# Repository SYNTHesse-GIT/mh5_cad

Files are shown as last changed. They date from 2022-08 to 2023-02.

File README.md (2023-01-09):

# mh5_cad - CAD files, including STLs for MH5 robot



The 3D design of the robot is maintained in [onshape](https://cad.onshape.com/documents/1b88afa68bb97584375e284c/w/8d3aebf9e78687fc1b4a5d80/e/6f5b4ad05cdba68c2c42dd17).

The parts bellow are for the Revision F model of the MH5 humanoid robot.

## Printing BOM

| Item | Description | Final | Qty | Comments |
|---|---|---|-----|---|
| [Foot-Sole](STL/Foot-Sole.stl) | Sole for the FSR feet | Yes | 2 | one for each foot
| [Foot-Top](STL/Foot-Top.stl) | Upper part of FSR feel | Yes | 2 | one for each foot
| [Foot-Back](STL/Foot-Back.stl) | Back side of the FSR foot, uses magnets | Yes | 2 | one for each foot
| [Ankle](STL/Ankle.stl) | Frame for ankle | Yes | 4 | 2 for each foot
| [MH5-F02](STL/MH5-F02.stl) | Stright U frame | Yes | 4 | 2 used in feet (1 each) and 2 used in arms (1 each)
| [MH5-F03](STL/MH5-F03.stl) | Bottom of servo frame | Yes | 6 | 3 for each arm
| [MH5-F04](STL/MH5-F04.stl) | Curved U frame | Yes | 4 | 2 used in hips and 2 in shoulders
| [MH5-F05](STL/MH5-F05.stl) | Thigh frame | Yes | 2 | one in each foot
| [Hand-Left](STL/Hand-Left.stl) | Anatomic left hand | Yes | 1 |
| [Hand-Right](STL/Hand-Right.stl) | Anatomic right hand | Yes | 1 |
| [Chest](STL/Chest.stl) | Chest main frame | Yes | 1 |
| [Front](STL/Front.stl) | Front chest cover | Yes | 1 |
| [Neck](STL/Neck.stl) | Neck | Yes | 1 |
| [Head-Back](STL/Head-Back.stl) | Back side of the head | Yes | 1 |
| [Head-Front](STL/Head-Front.stl) | Front side of the head | Yes | 1 |
| [Head-Camera-Cover](STL/Head-Camera-Cover.stl) | Cover for cameras. | Yes | 2 | One for each mini camera

## Assembly preparation

Before assembly you must configure the Dynamixel Servos as described in [Configuring servos](DOCS/servos.md).

You should also get familiar with the [installation of heat-serts](DOCS/assembly-heatserts.md). There will several steps in the following instructions where you will have to perform this activity.

Quite a few number of servos in this robot make use of the new through-the-idler wiring of the cables that produces a tidier cabling and reduces the stress and the risk of cables being severed by frame collision. You should be familiar with the instructions provided by Robotis for both the [XL430](https://emanual.robotis.com/docs/en/dxl/x/xl430-w250/#idler-horn-assembly) and the [2XL430](https://emanual.robotis.com/docs/en/dxl/x/2xl430-w250/#idler-horn-assembly) servos.

## Sub-groups Assembly

[**Leg assembly**](DOCS/assembly-legs.md) is almost identical for left and right because the 2-axis servomotors make impossible mirror assembly. The only difference is the way the feet are connected to the ankles and this is explicitly described in the instructions.

[**Arms assembly**](DOCS/assembly-arms.md) is symmetrical so that cables are following a consistent pattern (on the inside or on the outside of the assembly, but similar between left and right). The instructions describe these activities in detail.

[**Torso and neck**](DOCS/assembly-torso.md) assembly describes the assembly of the fixed components to the torso.

In [**Full assembly**](DOCS/assembly-full.md) the sub-assemblies prepared earlier as well as the electronic components are put together to produce the full robot.

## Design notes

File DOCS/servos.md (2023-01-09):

# Configuring servos

Before assembling the robot, all servos need to be configured. Because they come with the same pre-configured IDs, once connected on a chain the servos cannot be accessed because of duplicate IDs. Therefore is it very important to update the IDs of all the servos *before* they are mounted on frames and connected with the cables. In addition to IDs we will also change the communication speed and a small amount of other parameters to simplify their management after assembly in the robot.

We use two models of Robotis servos: [XL430-W250](https://emanual.robotis.com/docs/en/dxl/x/xl430-w250/) and [2XL430-W250](https://emanual.robotis.com/docs/en/dxl/x/2xl430-w250/). Logically the two servos have identical control characteristics, with the main difference that 2XL430 has a dual axis construction, behaving as two XL430 servos in one. Most of the control registers are therefore presented in duplicate, one for each axis, with a few notable exceptions that we will highlight in the following instructions.

## Connecting the servos

In order to configure the servos we will use the [DynamixelWizard2](https://emanual.robotis.com/docs/en/software/dynamixel/dynamixel_wizard2/) application provided by Robotis. The application is available for Windows, Mac and Linux operating systems and should be downloaded and installed according to the instructions provided in the link above.

To connect the servos to the computer we recommend using an interface like [U2D2](https://emanual.robotis.com/docs/en/parts/interface/u2d2/) that connects to computers using standard USB ports and provides high-speed Dynamixel ports compatible with all Robotis servos.

> **Note:** <br>
> U2D2 does not provide power to the servos, only data control signals. In order to power the servos being configured you need to use an external power supply and an adapter board that makes that power available over the Dynamixel bus. Our recommendation is to use the [U2D2 Power Hub](https://emanual.robotis.com/docs/en/parts/interface/u2d2_power_hub/) which pairs conveniently with the U2D2 interface. Robotis also has a [Starter Set](http://en.robotis.com/shop_en/item.php?it_id=902-0161-200) that includes the U2D2 interface, the Power Hub and a 5A 12V power supply.

When configuring the servos, you should connect only one at a time, to avoid conflicts with duplicate IDs. Theoretically, once you have configured a servo, you could add a new by daisy-chaining it to the previous one as we're setting IDs above 10 and there will not be duplicates, but frankly there is no advantage for having multiple servos connected at this stage and you should anyway avoid constructing chains of more than 6 servos as you could experience a degradation of communication performance. We recommend connecting one servo for configuration and then removing it before connecting the next servo.

To connect the servos follow the diagram below:

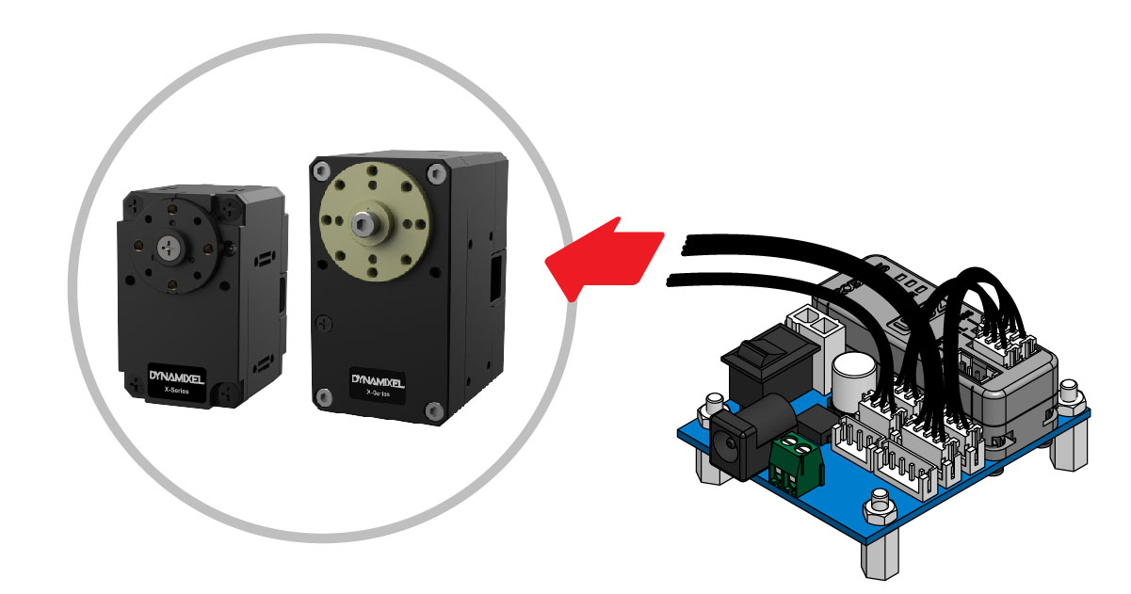
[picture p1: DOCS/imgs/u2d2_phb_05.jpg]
Connecting Servos


Servos have two connectors and any of them can be used to connect to the U2D2 interface.

The power supply should be connected to the DC plug on the Power Hub. The servo will indicate that has powered and is initialized successfully by short blinking the LED once. This LED should not be on continuously.

## DynamixelWizard setup

When first using the Dynamixel Wizard you will have to configure several settings like the communication port and the speed. Click the "Options" button in the toolbar:

Options

This will open the following dialog window:

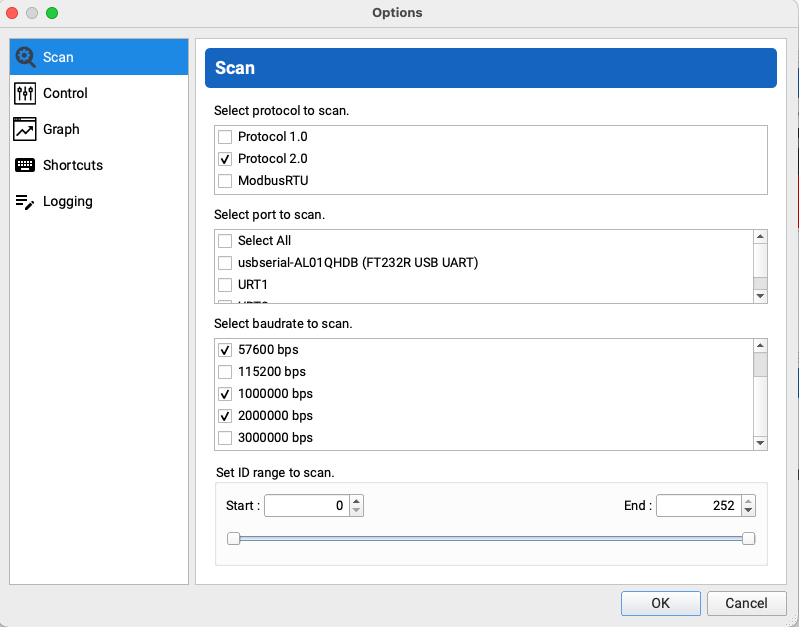
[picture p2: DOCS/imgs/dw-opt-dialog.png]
Options Dialog


In this window we will specify the following:

* **Protocols:** we will only use Protocol 2.0 as both models of servos come pre-configured with this communication protocol. For more details on what this protocol means you can read the excellent [documentation](https://emanual.robotis.com/docs/en/dxl/protocol2/) provided by Robotis.
* **Port:** you should make sure that the port that generated when connecting the U2D2 over the USB is checked. Depending on the platform you can identify the port by simply running DynamixelWizard first without the U2D2 interface connected and then with the interface connected. The additional port that is shown when the interface is connected is the one that should be checked in the dialog.
* **Baudrate:** before configuring a servo the application needs to scan the bus and identify all the servos that are connected. Servos come pre-configured with a communication speed of 57,600 bps, so this speed should be clicked on the dialog. We will configure the servos to work at 2Mbps, so this option should also be selected in the dialog. Other speeds are not necessary and should be deselecting. Selecting additional speeds will increase the time that the application will spend to scan the bus, because it will probe for all IDs in the range (specified a little bit later in the dialog) for all communication speeds. If we are sure that we do not have to work with any other speeds we can exclude them from scanning, thus reducing the amount of time is spend during this process. If you are unsure or you have problems with servos that are not detected during scanning (for instance servos that have been used previously in other projects and were configured with other communication speeds) you can activate additional communication speeds.
* **ID range:** the new servos come with a pre-allocated number 1 for XL430 and 1 and 2 for 2XL430. We will assign IDs in the range 11 through 52 for our robot, so we could enter an interval 0 through 60 in this section to reduce the amount of time spent on scanning the bus. Similar to the comments earlier about the communication speed, if the servos have been previously used and configured with IDs higher than that you would need to extend the range to include them. If unsure, expand the range from 0 to 252 (max ID), although you will see an proportional increase in scanning time.

Once you finished updating the settings, press the "Scan" button. A progress dialog box will be displayed showing all combinations of settings used in scanning. If a servo is detected it will immediately be shown on the left side of the window, together with all the related details. For instance this is how an XL430 will be shown:

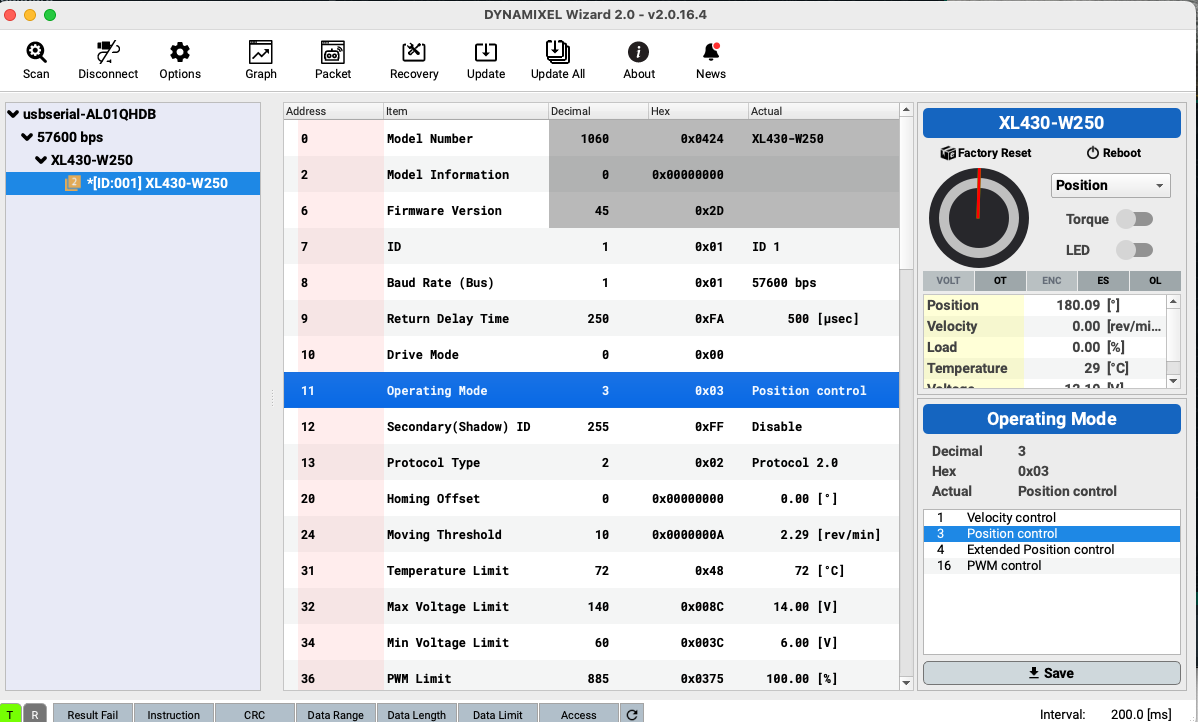
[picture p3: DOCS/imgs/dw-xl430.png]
XL430


And this is an 2XL430 shown in the application. You can see that it will appear as two separate IDs:

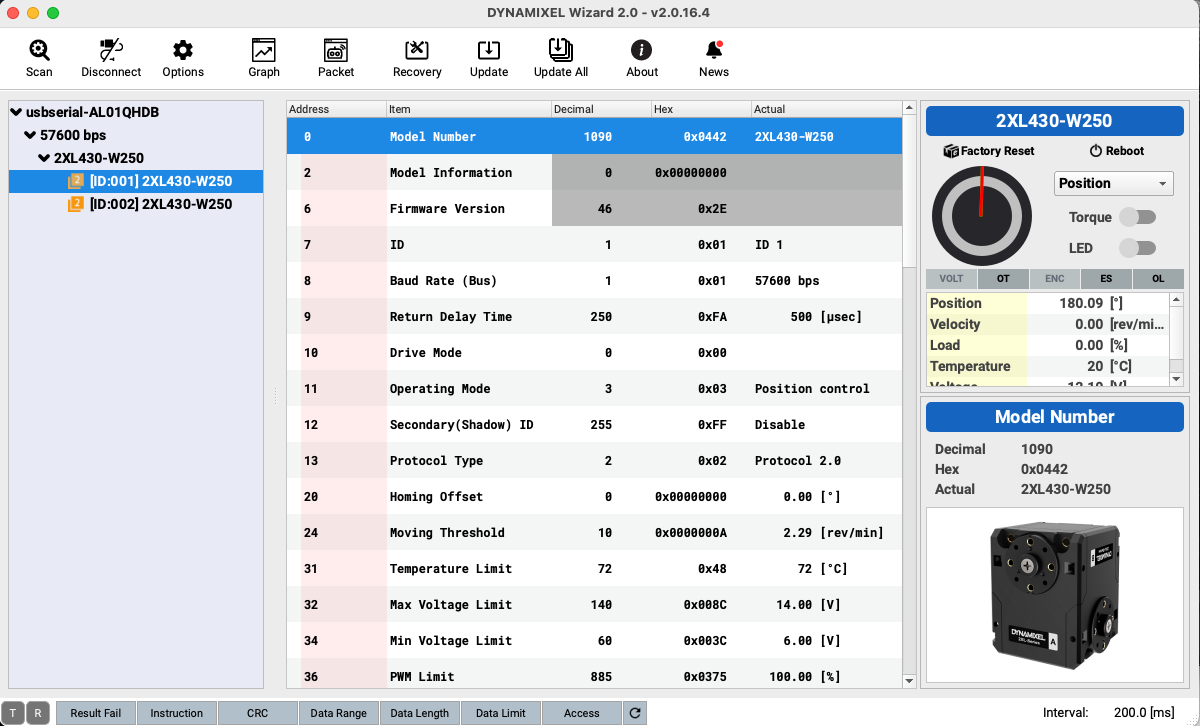
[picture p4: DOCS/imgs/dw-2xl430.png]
2XL430


> **Note:**
> A star (*) next to the ID of a servo indicates that there is a firmware update for that device. If that is the case it is highly recommended to perform this firmware update before doing the rest of the configuration changes. You can perform this update by choosing the "Update" button in the toolbar and following the instructions:
>
> Update

## Configuring IDs

To change the ID of a servo, select the register at address 7 called ID in the list in the center of the screen:

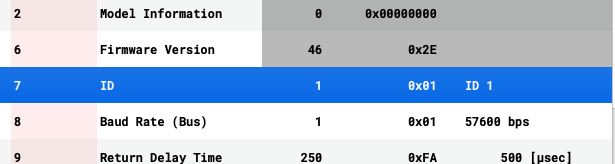
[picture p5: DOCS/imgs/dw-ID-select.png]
ID Select


On the right side select the new ID code from the list shown. The codes to change to are listed in the section [IDs used by Miha](#ids-used-by-miha) bellow. When finished press the "Save" button:

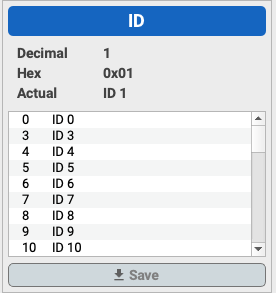
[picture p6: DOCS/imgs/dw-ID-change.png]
ID Change


The changed ID should be immediately reflected on the left side where the devices are listed.

For 2XL430 servos you need to perform the change for each axis.

When you have finished all the configurations and remove the servo from the bus you should affix a number sticker on the servo to keep track of their numbers. You can use for example these types of stickers:

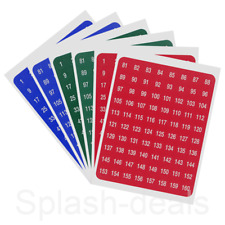
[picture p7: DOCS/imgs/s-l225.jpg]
Stickers


For XL430 the stickers can be applied anywhere on the body of the servo, although we recommend to place them on the bottom side as they will be less visible once the servos are integrated in with the frames. For 2XL430 servos you you will have to apply two stickers (one for each axis) and is recommended to place them on the reserved placeholders marked ID (A) and ID (B) as per the specifications of the table below. Note that the makers are exactly opposite to the horn representing that ID for this type of servos. When assembling the servos later it will be important to orient them according to the axis intended for that joint and we will use the IDs to identify the correct axis that needs to be screwed on a particular frame.

## Configuring baudrate

As mentioned earlier these servos will com pre-configured at 57,600bps communication speed. FOr a more efficient communication we will have to change the speed to 2Mbps and it is significantly easier to this at this moment, rather than later when servos are in mounted in the robot.

To change the communication speed select register with address 8 (Baud Rate):

Baud Select

On the right side of the window the application will provide a convenient list of possible communication speeds that can be set for this device, according to the technical specs of the device. It will also conveniently convert between the internal representation of the communication speed to the clear representation in human readable form:

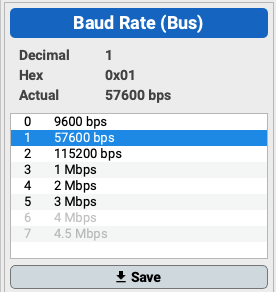
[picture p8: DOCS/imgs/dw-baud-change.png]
Baud Change


In our case select the code 4 (representing 2Mbps speed) and press "Save". The change will be immediately visible on the left tree as long as the communication speed of 2Mbps has been included in the Options as described earlier in these instructions.

For 2XL430 servos you only need to make this change for one ID and both axes will inherit this setting (it is not possible for the axes to operate at different communication speeds).

## Other configurations

If you want you can also review and update other configuration items, although these are not that critical because the initialization procedures of Miha make sure that these settings are in place when starting up the robot.

| Value | Address | Default | New | Comments |
|---|---|---|-----|---|
|Return Delay Time | 9 | 250 | 0  | This parameter configures an extra delay before servos respond to a data request. Because we're using high speed communication this delay is not needed
| Drive Mode | 10 | 0 | 0 | The default of 0 should be used, but in certain circumtances the MH5 controllers might chose to configure the servos with other drive mode
| Operating Mode | 11 | 3 | 3 | This should be 3 (Position Control)

## Making sure that every thing works fine

Before disconnecting the servo and labeling it, you should also make sure that the servo works as expected and that the assignments of IDs are as intended.

In the list of registers select "Goal Position" at address 116:

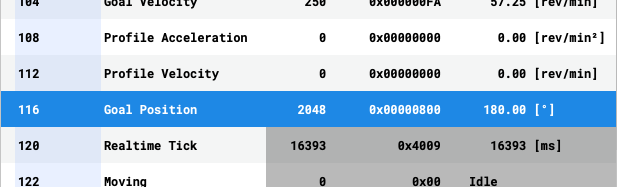
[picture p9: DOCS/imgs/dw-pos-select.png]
Goal Select


On the right side you will see a convenient interface that allows you to manually position the horn of the servo:

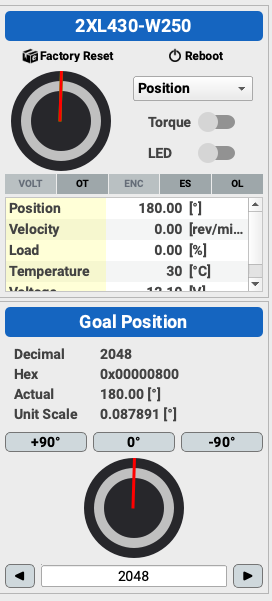
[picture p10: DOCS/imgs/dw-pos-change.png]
Goal Change


First toggle the Torque switch in the upper part of the interface. The horn should now be stiff and controllable. Use the +90 and -90 buttons to command the horn to move to the desired angles. Observe that the horn move smoothly and without any jitter. If using 2XL430 servo then also make sure that the correct horn is moving (should be the one opposite the label with the new ID assigned for that axis).

If everything is OK place the horn in the 0 position (press the 0 button) and then deactivate the torque for the servo. If using a 2XL430 repeat the process for the second ID.

## IDs used by MIHA

This section lists the IDs that need to be assigned to the servos for each joint of Miha robot. For joints that are implemented by using 2XL430 servos pay attention to the codes assigned to each axis.

<table>
    <thead>
        <tr>
            <th>Model</th>
            <th>Axis</th>
            <th>Def ID</th>
            <th>New ID</th>
            <th>Joint Code</th>
            <th>Joint Description</th>
    </thead>
    <tbody>
        <tr>
            <td rowspan=2>2XL430</td>
            <td>A</td>
            <td>1</td>
            <td>11</td>
            <td>l_ank_r</td>
            <td>Left Ankle Roll</td>
        </tr>
        <tr>
            <td>B</td>
            <td>2</td>
            <td>12</td>
            <td>l_ank_p</td>
            <td>Left Ankle Pitch</td>
        </tr>
        <tr>
            <td rowspan=2>2XL430</td>
            <td>A</td>
            <td>1</td>
            <td>13</td>
            <td>l_kne_y</td>
            <td>Left Knee Yaw</td>
        </tr>
        <tr>
            <td>B</td>
            <td>2</td>
            <td>14</td>
            <td>l_kne_p</td>
            <td>Left Knee Pitch</td>
        </tr>
        <tr>
            <td rowspan=2>2XL430</td>
            <td>A</td>
            <td>1</td>
            <td>15</td>
            <td>l_hip_p</td>
            <td>Left Hip Pitch</td>
        </tr>
        <tr>
            <td>B</td>
            <td>2</td>
            <td>16</td>
            <td>l_hip_r</td>
            <td>Left Hip Roll</td>
        </tr>
        <tr>
            <td rowspan=2>2XL430</td>
            <td>A</td>
            <td>1</td>
            <td>21</td>
            <td>r_ank_r</td>
            <td>Right Ankle Roll</td>
        </tr>
        <tr>
            <td>B</td>
            <td>2</td>
            <td>22</td>
            <td>r_ank_p</td>
            <td>Right Ankle Pitch</td>
        </tr>
        <tr>
            <td rowspan=2>2XL430</td>
            <td>A</td>
            <td>1</td>
            <td>23</td>
            <td>r_kne_y</td>
            <td>Right Knee Yaw</td>
        </tr>
        <tr>
            <td>B</td>
            <td>2</td>
            <td>24</td>
            <td>r_kne_p</td>
            <td>Right Knee Pitch</td>
        </tr>
        <tr>
            <td rowspan=2>2XL430</td>
            <td>A</td>
            <td>1</td>
            <td>25</td>
            <td>r_hip_p</td>
            <td>Right Hip Pitch</td>
        </tr>
        <tr>
            <td>B</td>
            <td>2</td>
            <td>26</td>
            <td>r_hip_r</td>
            <td>Right Hip Roll</td>
        </tr>
        <tr>
            <td>XL430</td>
            <td>-</td>
            <td>1</td>
            <td>31</td>
            <td>l_elb_p</td>
            <td>Left Elbow Pitch</td>
        </tr>
        <tr>
            <td>XL430</td>
            <td>-</td>
            <td>1</td>
            <td>32</td>
            <td>l_elb_y</td>
            <td>Left Elbow Yaw</td>
        </tr>
        <tr>
            <td>XL430</td>
            <td>-</td>
            <td>1</td>
            <td>33</td>
            <td>l_sho_r</td>
            <td>Left Shoulder Roll</td>
        </tr>
        <tr>
            <td>XL430</td>
            <td>-</td>
            <td>1</td>
            <td>34</td>
            <td>l_sho_p</td>
            <td>Left Shoulder Pitch</td>
        </tr>
        <tr>
            <td>XL430</td>
            <td>-</td>
            <td>1</td>
            <td>41</td>
            <td>r_elb_p</td>
            <td>Right Elbow Pitch</td>
        </tr>
        <tr>
            <td>XL430</td>
            <td>-</td>
            <td>1</td>
            <td>42</td>
            <td>r_elb_y</td>
            <td>Right Elbow Yaw</td>
        </tr>
        <tr>
            <td>XL430</td>
            <td>-</td>
            <td>1</td>
            <td>43</td>
            <td>r_sho_r</td>
            <td>Right Shoulder Roll</td>
        </tr>
        <tr>
            <td>XL430</td>
            <td>-</td>
            <td>1</td>
            <td>44</td>
            <td>r_sho_p</td>
            <td>Right Shoulder Pitch</td>
        </tr>
        <tr>
            <td rowspan=2>2XL430</td>
            <td>A</td>
            <td>1</td>
            <td>51</td>
            <td>head_p</td>
            <td>Head Pitch</td>
        </tr>
        <tr>
            <td>B</td>
            <td>2</td>
            <td>52</td>
            <td>head_y</td>
            <td>Head Yaw</td>
        </tr>
    </tbody>
</table>

The following picture shows the IDs of servos in the context of the robot:

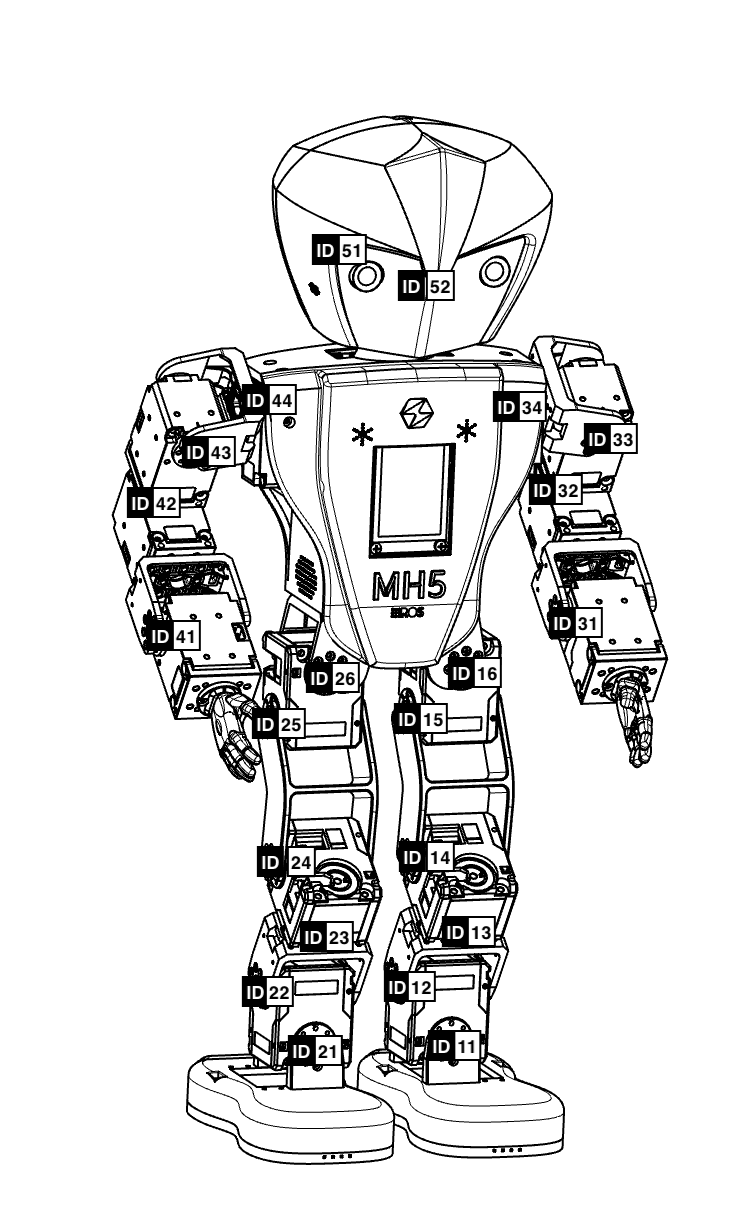
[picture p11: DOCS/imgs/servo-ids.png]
Robot Servos


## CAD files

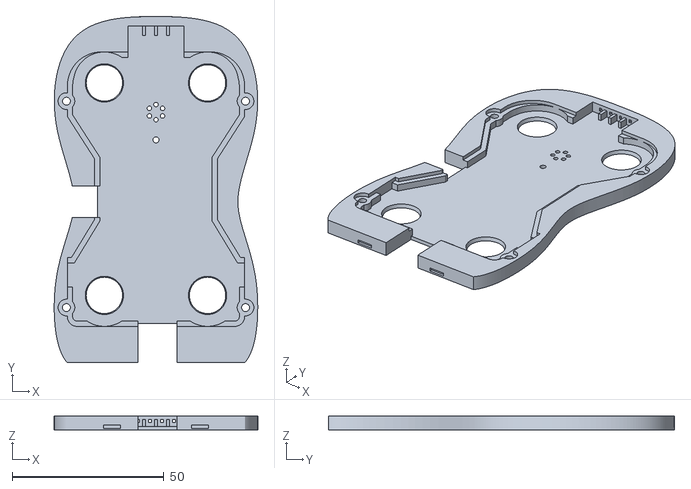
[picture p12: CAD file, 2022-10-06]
STL/Foot-Sole.stl
67.1 x 114.0 x 4.70

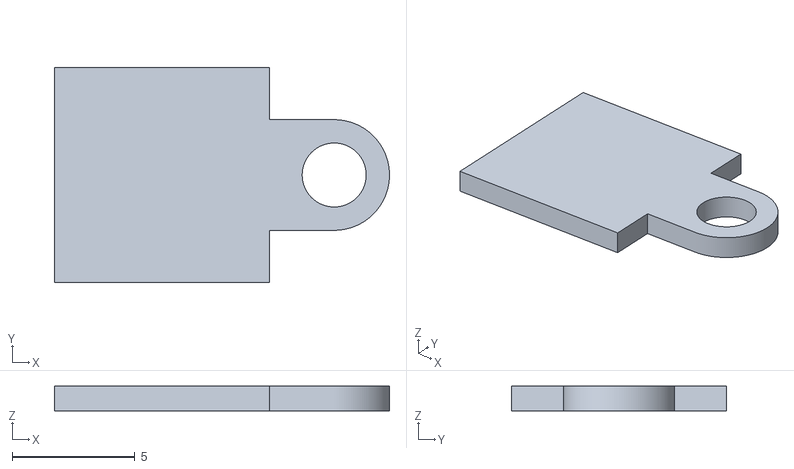
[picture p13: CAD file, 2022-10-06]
STL/Head-Camera-Cover.stl
13.6 x 8.75 x 1.00

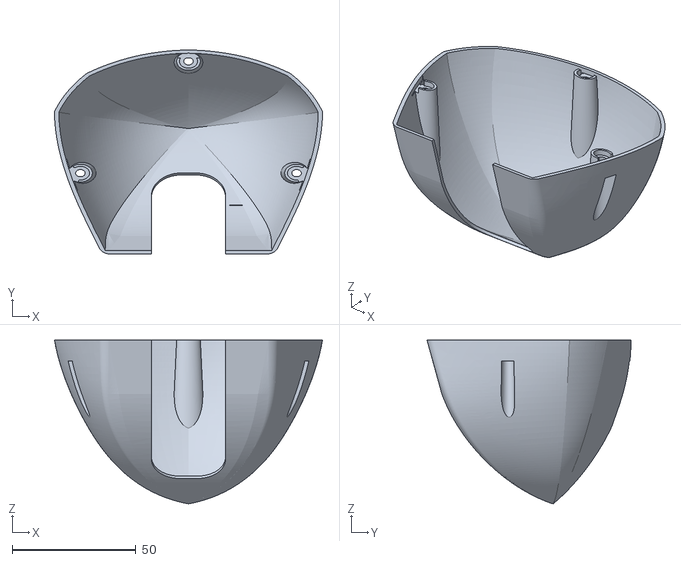
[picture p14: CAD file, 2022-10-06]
STL/Head-Back.stl
108.5 x 82.6 x 66.3

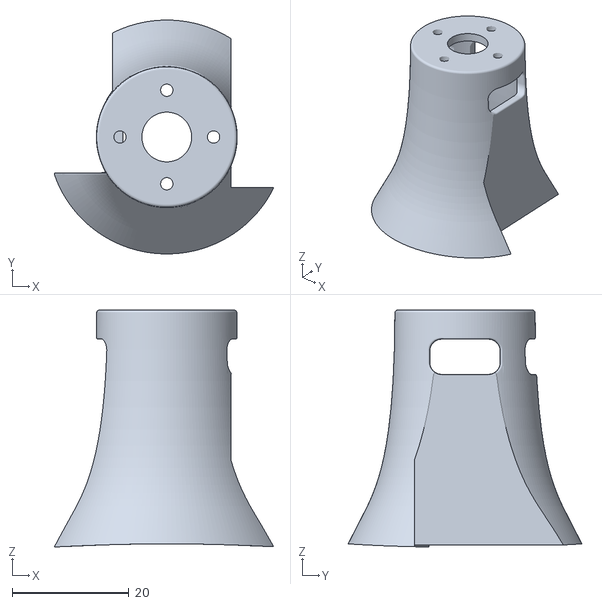
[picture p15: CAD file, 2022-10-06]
STL/Neck.stl
37.5 x 40.0 x 40.5

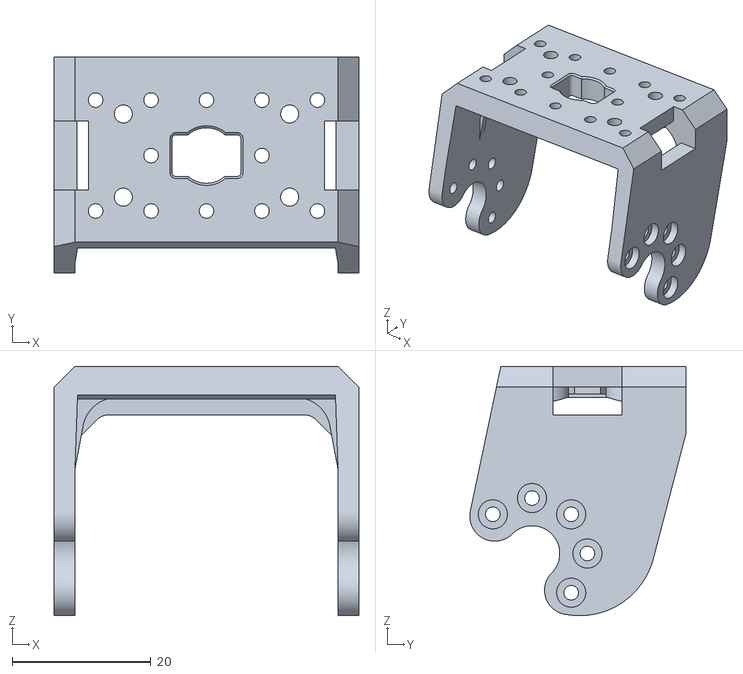
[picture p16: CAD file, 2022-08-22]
STL/MH5-F04.stl
44.0 x 31.2 x 36.0

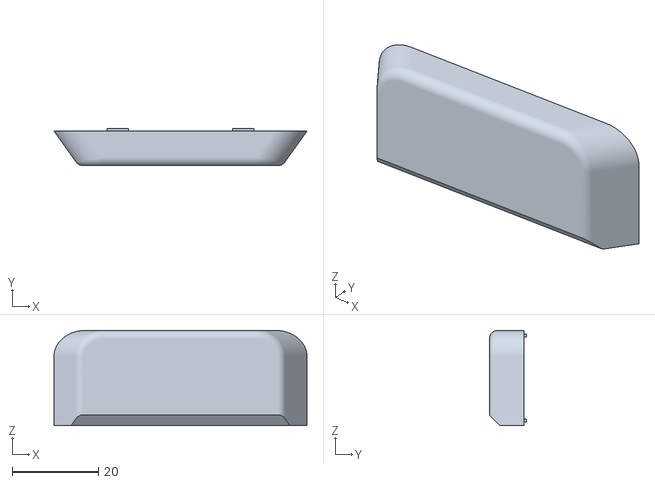
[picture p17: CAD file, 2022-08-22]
STL/Foot-Back.stl
58.5 x 8.65 x 22.1

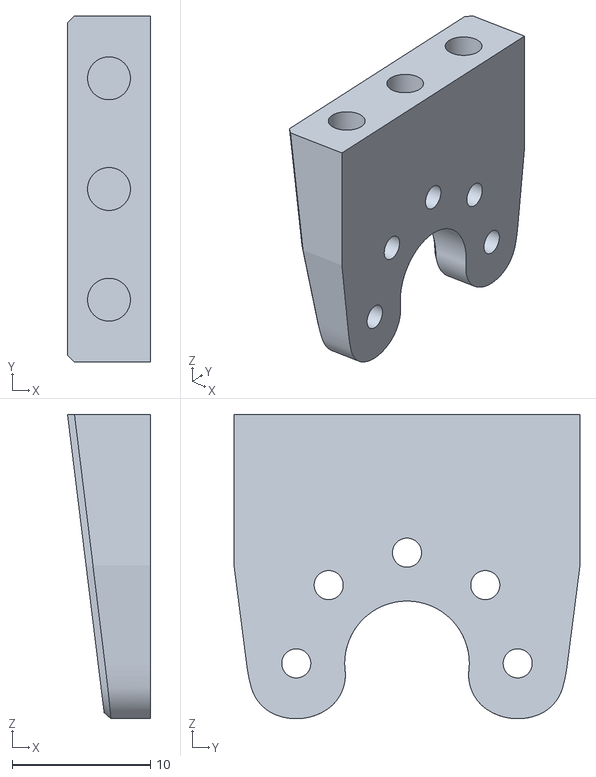
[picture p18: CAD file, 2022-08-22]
STL/Ankle.stl
6.00 x 25.0 x 22.0

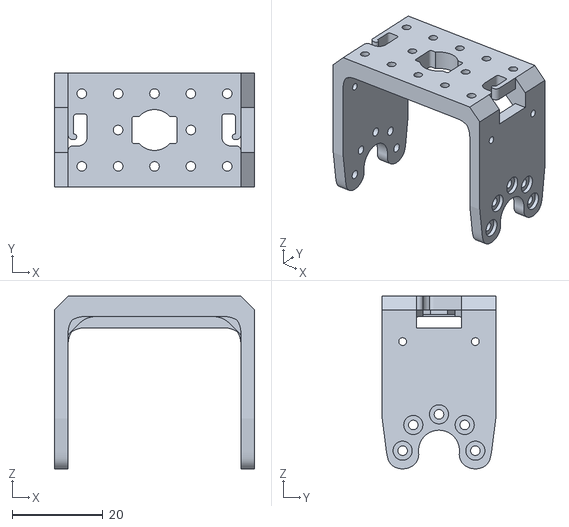
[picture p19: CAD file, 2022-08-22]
STL/MH5-F02.stl
44.0 x 25.0 x 38.0

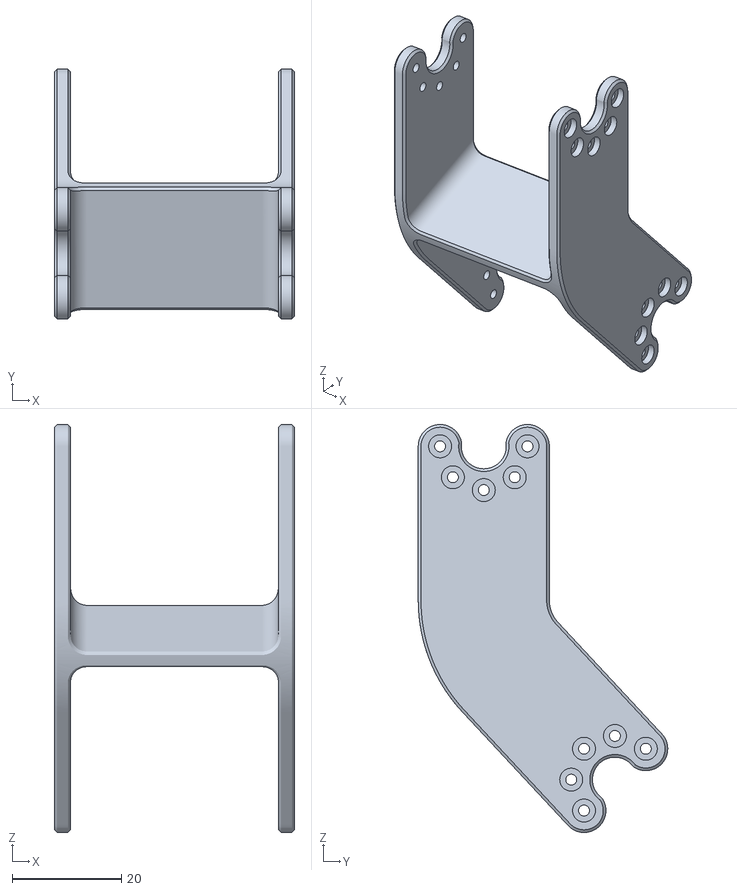
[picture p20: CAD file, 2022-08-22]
STL/MH5-F05.stl
44.0 x 45.7 x 74.7

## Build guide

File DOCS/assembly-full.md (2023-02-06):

# Full Assembly

After you have finished with the assembly of the [legs](assembly-legs.md), [arms](assembly-arms.md) and [torso](assembly-torso.md) you can now finalize the assembly by putting it all together and finishing the remaining tasks.

## Arms Assembly

### Step 1

Take the right arm and place it over the supports in the torso. Make sure that the long Dynamixel cable that runs from the lower connector in Servo ID 31 to the shoulder servo ID 32 is routed between the lower supports and the edge of the torso frame. Use 8 M2.6 self-tap screws (black) to secure the servo in position: 2 on the top, 2 on the bottom and 4 on the back. The screws should make their way into the plastic case of the servo and provide additional strength to the torso frame.

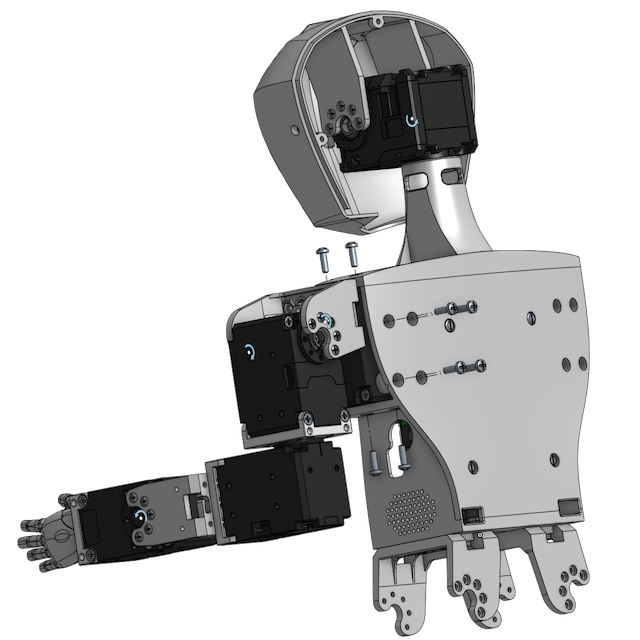
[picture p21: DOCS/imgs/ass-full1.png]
left-arm


### Step 2

Repeat the process above with the right arm:

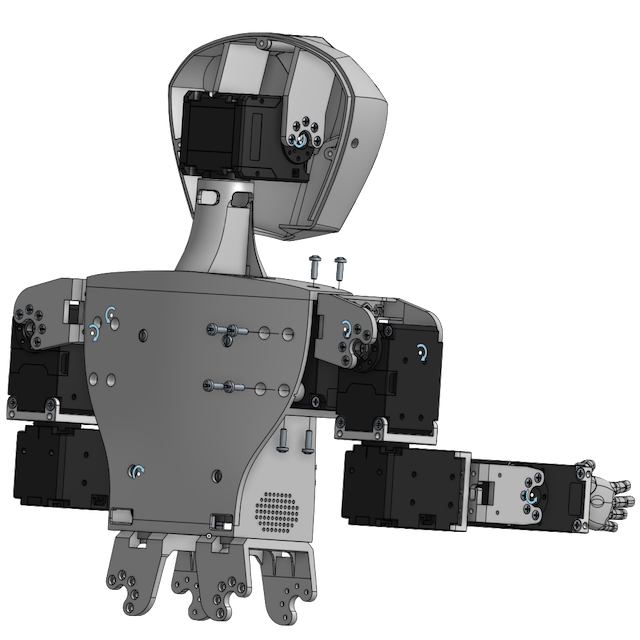
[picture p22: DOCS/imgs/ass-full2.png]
right-arm


You can now connect the two short Dynamixel cables from the shoulder servos to the second and third connectors in the HAT board (the first connector is used by the cable coming from the head servo). It doesn't matter which way they are connected.

## Legs Assembly

### Step 3

Take the left leg assembly and place it in the hip frame. Use 5 M2x5mm screws to connect the horn and another 5 to connect the idle on the back. The servo should be vertical when connected to the frame.

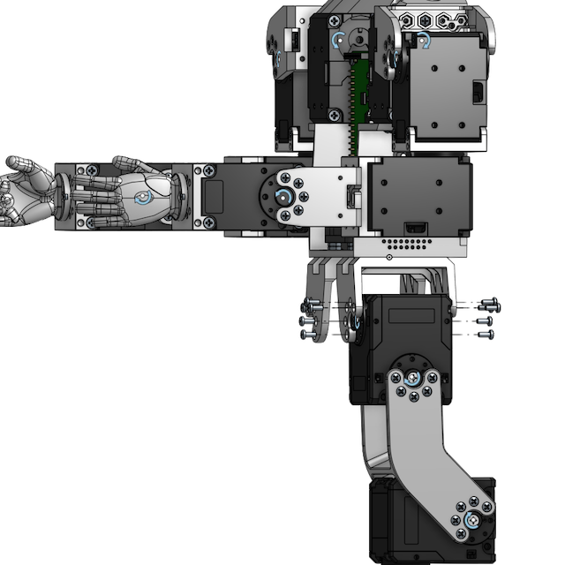
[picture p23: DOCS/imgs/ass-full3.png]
left-leg


### Step 4

Repeat the steps for the right leg and secure it in position with 5 M2x5mm screws in the front and 5 in the back.

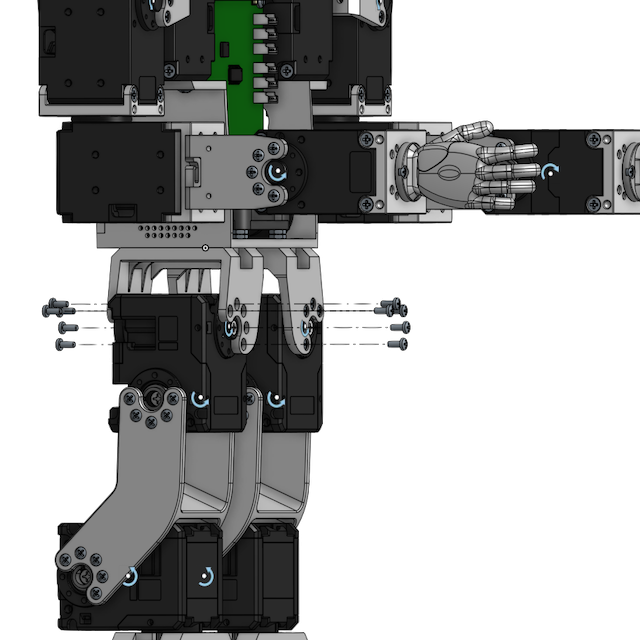
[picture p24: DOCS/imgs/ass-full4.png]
right-leg


You should now take the long Dynamixel cables coming out of the idles of the top hip joints and route them through the holes that are in the lower side of the torso. Carefully pull the cables towards the frond between the speakers and the fan on either side. Then connect the cables to the lower two connectors in the HAT board.

## Front Assembly

### Step 5

Place the [2.4 inch TFT display](https://www.waveshare.com/product/displays/lcd-oled/lcd-oled-3/2.4inch-lcd-module.htm) on the [front frame](../STL/Front.stl) positioning it with the JST connector down. Use 4 sepf-tap M2 screws to secure the display in position.

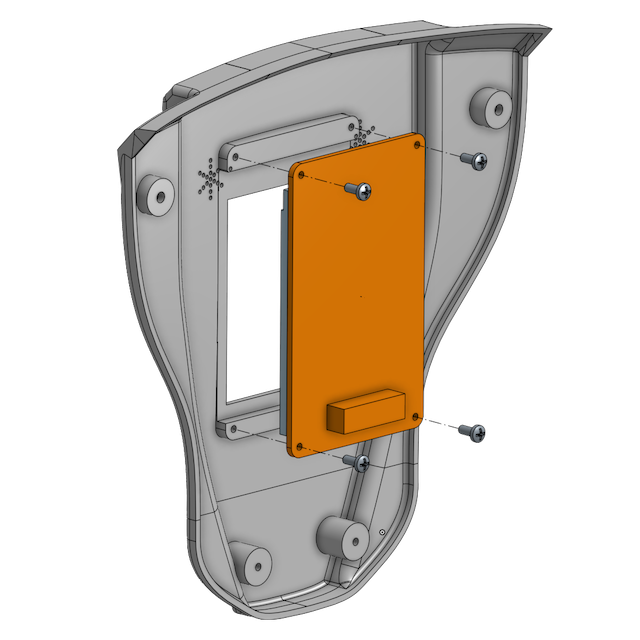
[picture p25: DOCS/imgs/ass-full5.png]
screen


### Step 6

Connect the display cable from the HAT board to the display and then place the front over the chest and using 2 M2.5 self-tap screws fix the chest onto the holes in the hip servos.

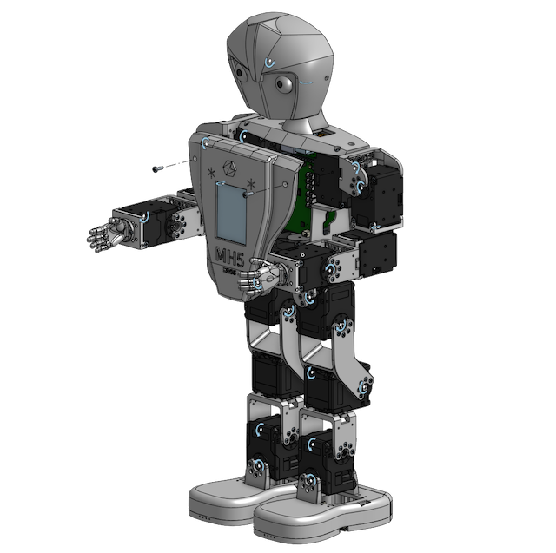
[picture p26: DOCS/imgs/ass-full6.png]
front


## Head Assembly

### Step 7

The final step is to place the [head back](../STL/Head-Back.stl) onto the front head and to fix it in position with 3 M2.5 self-tap screws.

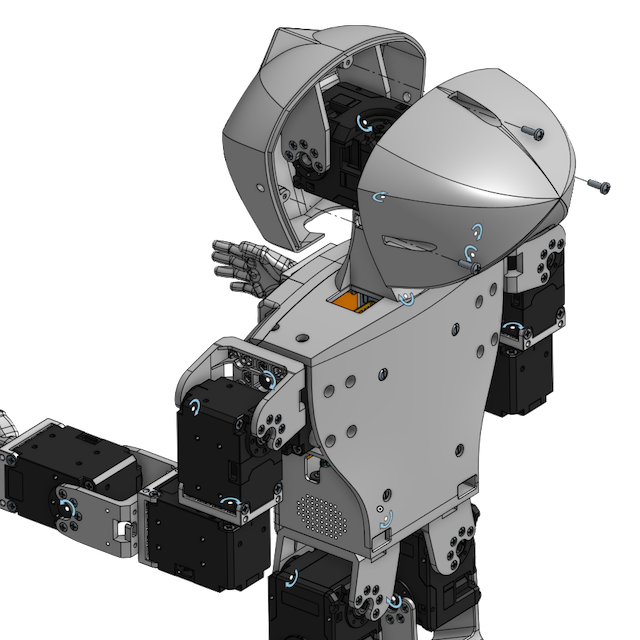
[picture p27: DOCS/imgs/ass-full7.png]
head-back


This concludes the assembly of the MH5 robot. Before starting to use the robot you should perform a check of the robot assembly. This check makes sure that the servos are configured correctly and mounted in the correct position without activating them and thus risking commands that would put the motors or frames at risk.

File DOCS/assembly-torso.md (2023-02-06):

# Torso and Head Assembly

Torso and head are assembled together. For these parts the electronic components (cameras, Raspberry Pi, HAT, etc.) also play and important role and you should pay attention at the order of assembly as some electronic components are difficult to install if the order is not followed.

## Head assembly

### Step 1

First install 3 heat-serts into the [neck frame](../STL/Neck.stl) as shown in the following figure, following the instructions about [inserting the heat-serts](./assembly-heatserts.md):

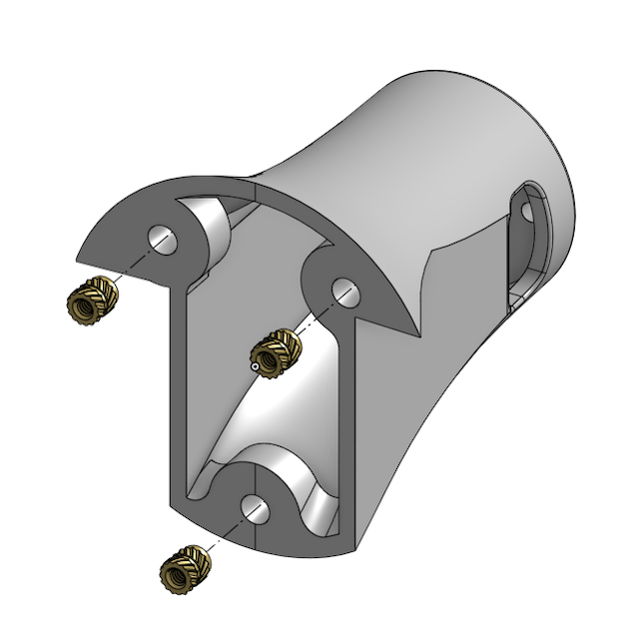
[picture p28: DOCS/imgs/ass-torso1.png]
neck


### Step 2

Use the neck servo with IDs 51/52 and assemble an idle on the Axle B (52). You do not need to assemble an idle on the Axis A (51) and you do not need to mount a cable through the idle. For this servo there will be one cable only and this will be mounted freely into the connector a little bit later.

Use 4 M2x5 screws to mount the horn of Axis A (51) onto the top of the neck frame, making sure that the servo is positioned as in the figure with the Axis B towards the front of the neck. It might be a little tricky to place the screws in position, using a magnetic screwdriver would help with this task.

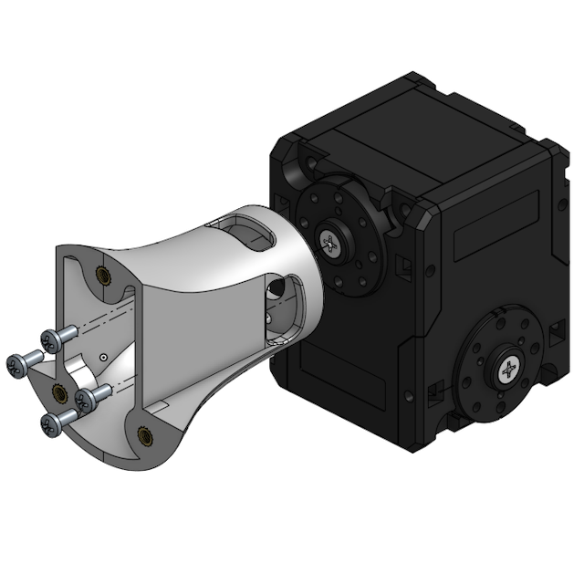
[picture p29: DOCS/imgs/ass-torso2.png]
neck-servo


Use an 180mm Dynamixel cable and connect it on the side connector of the servo, then guide the cable through the middle hole of the neck and pull is towards the base of neck all the way. Make sure that there is enough cable between the whole in the neck and the servo so that the servo can move freely 90 degrees left and right without limitations.

Place the 2 [Waveshare mini cameras](https://www.waveshare.com/product/raspberry-pi/cameras/rpi-fpc-camera.htm), one at the time, through the base of the neck and using plastic tweezers pull them through the side holes in the beck, one on the left side and one on the right side. It would be helpful to note on the FPC connector which one is Left and which Right, so that you know how they will be later connected to the CSI connectors on the Cm4 carrier board.

### Step 3

Place each camera into the appropriate position in the [head front frame](../STL/Head-Front.stl) with the flat cable positioned upwards. Place over the cameras the [camera cover](../STL/Head-Camera-Cover.stl) and secure it in position with one self tap M2 screw.

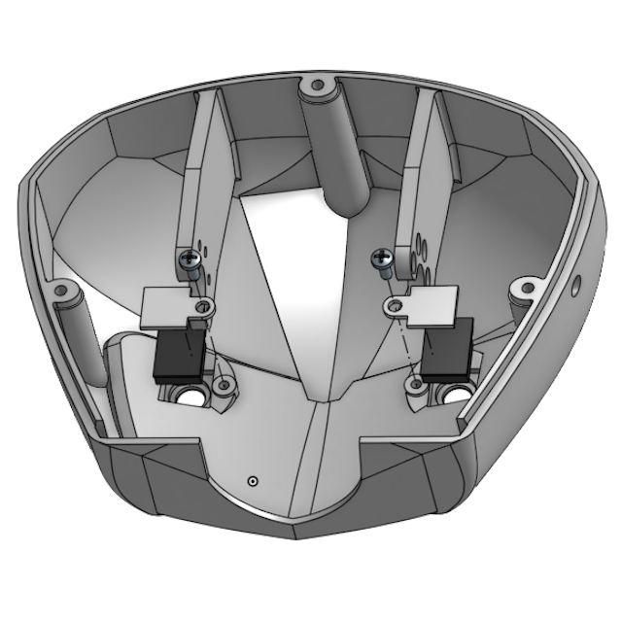
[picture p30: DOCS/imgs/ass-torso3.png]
front-head


### Step 4

Now place the head front over the horn and idle of the head servo Axle B and secure it in place with 5 M2x5mm screws on one side and another 5 on the other side. Use the holes in the side of the head frame to position the screwdriver in a convenient position and to be able to tighten the screws.

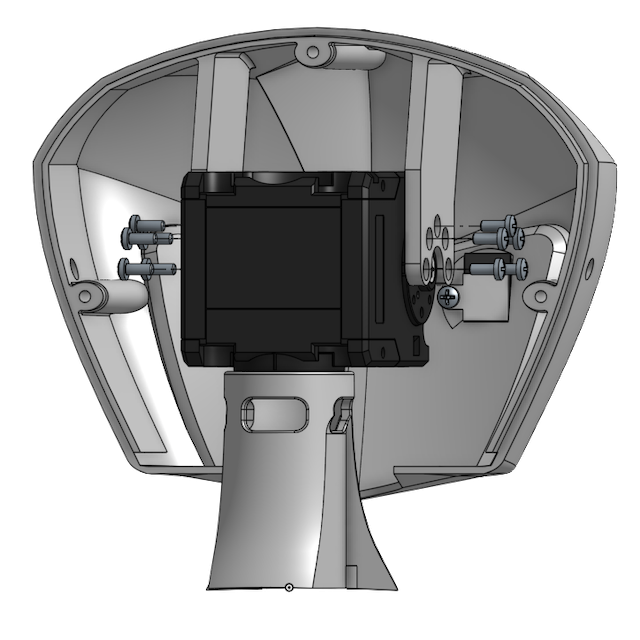
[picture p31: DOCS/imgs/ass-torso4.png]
front-plus-neck


## Torso Assembly

### Step 5

Place the neck and front head assembly over the [chest frame](../STL/Chest.stl) and secure it with 3 M2x5mm screws. Make sure the Dynamixel cable and the two FPC camera cables are coming through the middle cutout in the chest clean without being obstructed.

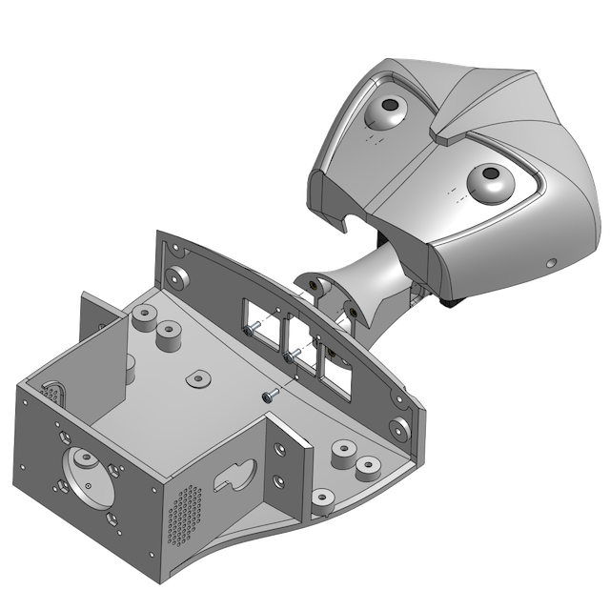
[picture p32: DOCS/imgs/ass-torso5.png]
chest-plus-neck


### Step 6

Place 4 M2 nuts in the outer recesses in the lower plate of the chest as shown in the figure:

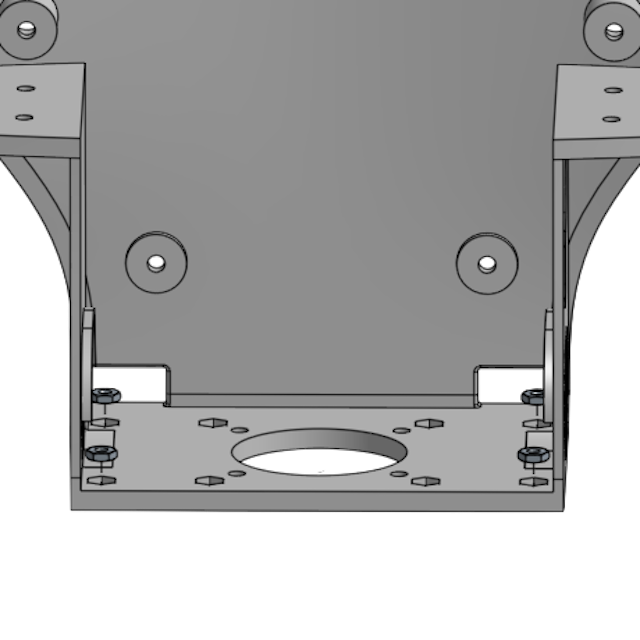
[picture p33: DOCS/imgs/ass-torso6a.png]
lower-chest-nuts


Then place 2 [F04](../STL/MH5-F04.stl) frames so that they point downwards and to the exterior and fix them in place with 4 M2x5mm screws against the nuts that you installed earlier:

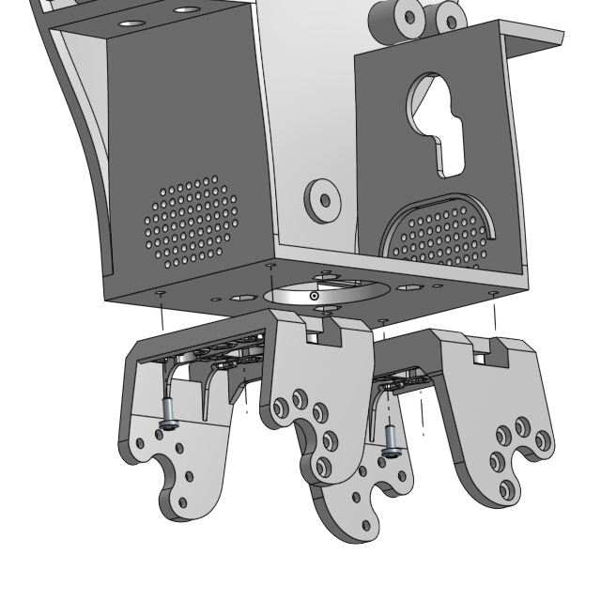
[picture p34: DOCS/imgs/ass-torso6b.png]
lower-chest-hips


### Step 7

If you are installing speakers, then you can place them now in the designated spaces. Remove the adhesive cover from the front of the speaker and place them with the cable facing the front of the robot in the designated positions:

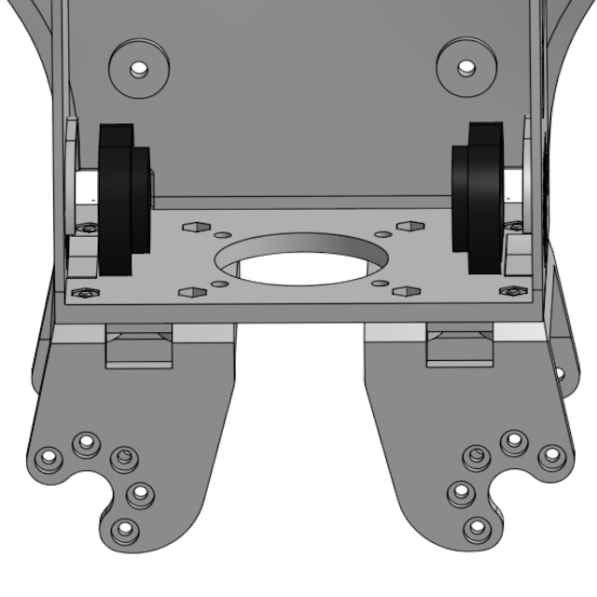
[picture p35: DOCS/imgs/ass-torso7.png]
speakers


### Step 8

We will now mount the [4010 PWM fan](https://www.waveshare.com/fan-4010-pwm-12v.htm) in the lower part of the torso.

Insert 4 M2x20mm long screws from the hip frames (F04) upwards then place 2 M2.5 nuts (can be plastic nuts) on top to act as a spacer between the fan and the bottom of the chest frame. Then place the fan through the 4 screws orienting the cables on the rear part of the chest and with the writing facing down (this ensures that the flow of air is from the chest towards outside). Finish with 4 M2 nuts inserted in the upper recess of the fan and tighten the screws.

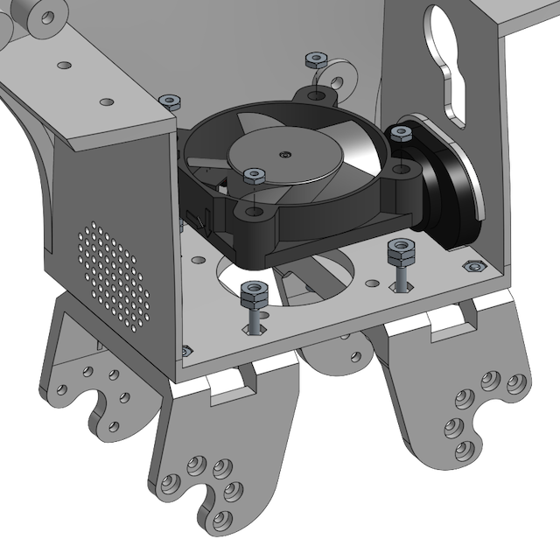
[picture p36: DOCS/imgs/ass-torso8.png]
fan


## Electronics

We will now assemble the electronics and connect the cameras to the CM4 carrier board.

### Step 9

First install the heat sink on the Cm4 module following the [instructions](https://www.waveshare.com/product/cm4-heatsink.htm) from the manufacturer.

Install the CM4 onto the [Waveshare IO carrier board](https://www.waveshare.com/product/raspberry-pi/boards-kits/compute-module-4-cat/cm4-io-base-b.htm). Add a WiFi USB dongle in the lower USB connector:

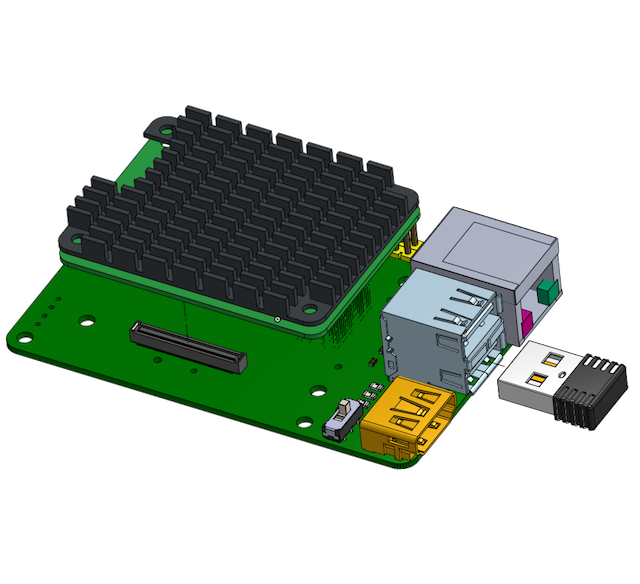
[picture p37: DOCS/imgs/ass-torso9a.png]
CM4-assembly


Place 4 M2.5x6mm male-female standoffs on the underside of the IO carrier board and screw 4 M2.5x20mm female-female standoffs on the upper side of the carrier board:

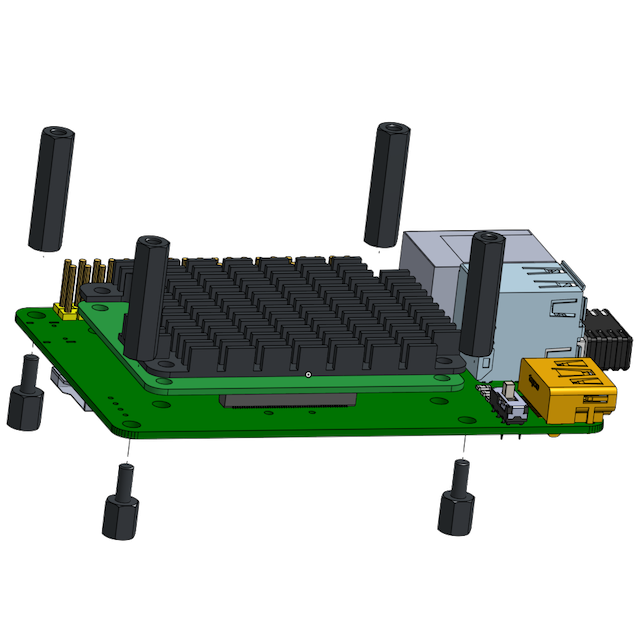
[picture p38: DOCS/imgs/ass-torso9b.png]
standoffs


The board is ready to be inserted in the torso.

### Step 10

Carefully place the assembled IO carrier board and the CM4 into the torso. You will have to position the board at an angle with the USB connectors (and the WiFi) tilted first in, insert the WiFi into the hole in the torso and then let the board slide in and down. Make sure that:

* the fan cable is routed under the carrier board and then over the board between the USB and HDMI connector
* the WiFi dongle is aligned with the lower cutout in the top of the torso and slides inside the neck
* all cables from the neck are routed through the small notch above the second USB connector
* the 6mm standoffs are aligned with the holes in the back of the torso

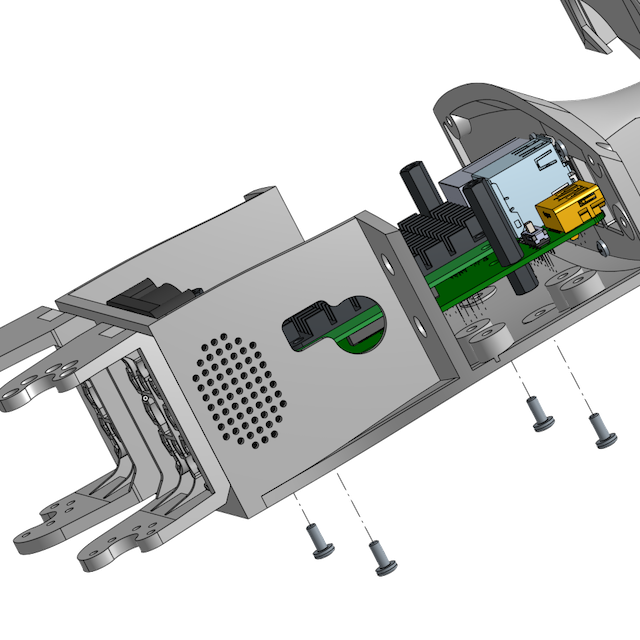
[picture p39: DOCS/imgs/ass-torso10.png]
torso-electronics


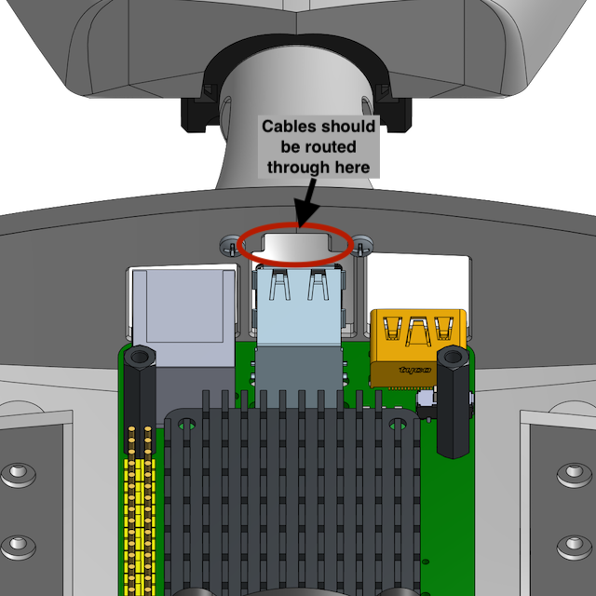
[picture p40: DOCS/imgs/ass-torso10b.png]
torso-notch-detail


Once the carrier board is secured in place connect the fan to the connector on the IO board. The fan operates 12V and connector on the carrier board only supplies 5V. Because of this the power pin (red) of the fan is separately connected to a JST EH 3 pin connector that will be connected separately on the HAT board.

Then, carefully, direct the camera flat connectors toward the two CSI connectors on the IO board and connect them. Place the cables flat over the CM4 heat-sink.

### Step 11

You can now place the MH5-HAT over the carrier board. This should be fixed with 4 M2.5x6mm (plastic) screws in the the hex standoffs.

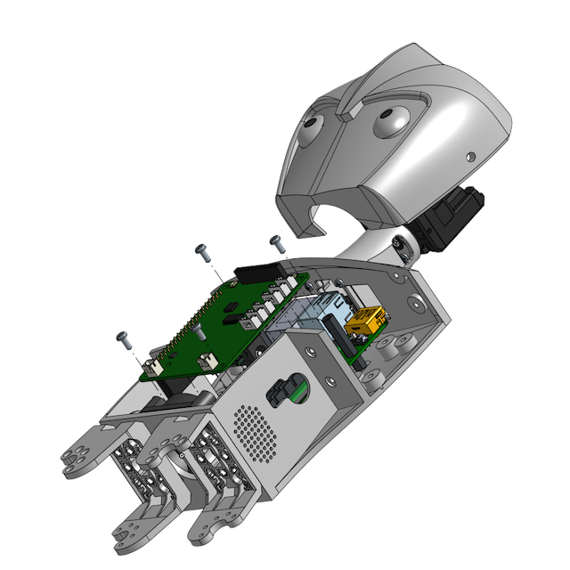
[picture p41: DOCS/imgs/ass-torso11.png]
torso-final


The HAT board has 6 Dynamixel connectors on the side (JST EH 3 pin) grouped in 2 sets of 3: the top 3 are for connecting the upper part of the body (head and arms) while the lower 3 are for the legs and to power the fan. At this moment you should have one Dynamixel cable coming through the neck for the head servo. Connect it to the topmost connector on the board. We will connect the cables from the arms later when the two pre-assembled arms are attached to the torso. Also you should take the red cable from the fan that is attached to a JST EH connector and connect it on the 4 connector from top (the first in the second set of 3 connectors). We will connect the cables from the legs once they are attached to the torso.

If you installed the speakers connect the cables (JST PH 2 pin) to the two connectors on the lower side of the HAT board, one on the left and one on the right.

This concludes the assembly of the torso. The final activities will be to assemble together the legs and arms onto the torso and complete the robot with the front frame and the back of the head frame. You can find these instructions in [here](assembly-full.md).

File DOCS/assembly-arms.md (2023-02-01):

# Arms Assembly

## Arm Assembly

This section presents the steps needed to assemble MIHA arms. They are similar between the left and right side with certain differences that the instructions will highlight. If no specific differentiation is provided, the instructions are assumed to be the same for both sides.

### Step 1

Begin by assembling the hands to a bottom of servo frame [F03](../STL/MH5-F03.stl). For left arm use the [Hand left](../STL/Hand-Left.stl), and for right arm use the [Hand right](../STL/Hand-Right.stl). Assemble them using 2 M2 screws and 2 nuts. Nuts should be positioned on the inside of the F03 frame and the screws should be placed through the two holes in the hand frames. The F03 frame should be as in the images bellow:

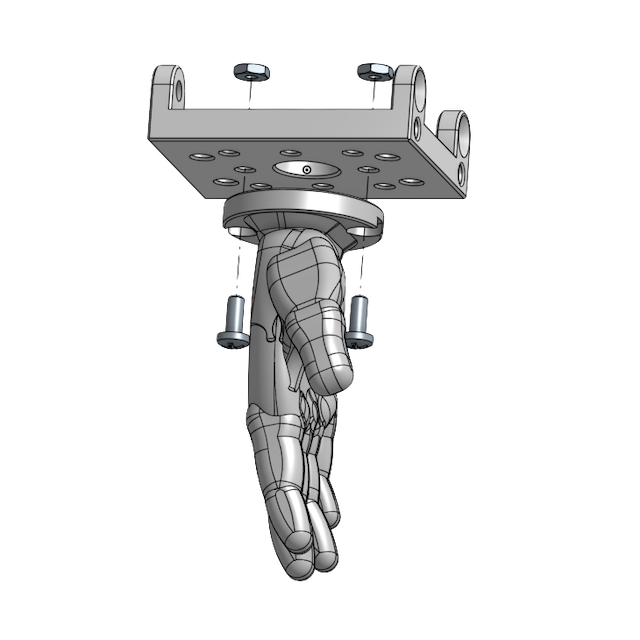
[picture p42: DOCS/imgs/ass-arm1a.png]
handr


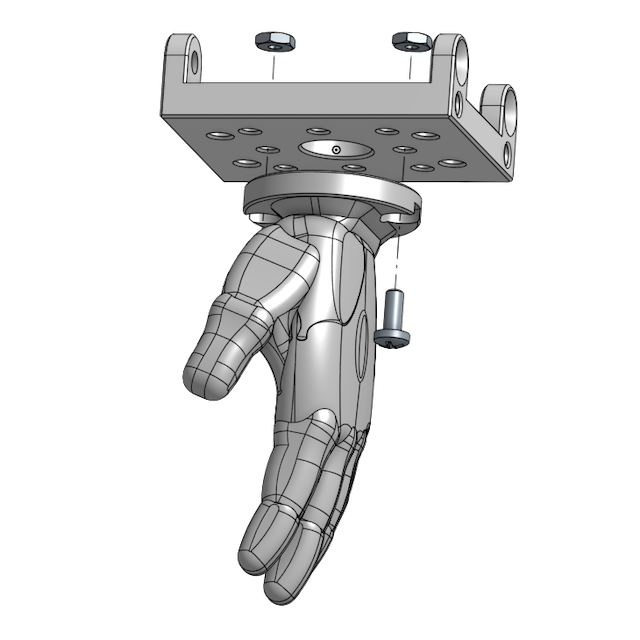
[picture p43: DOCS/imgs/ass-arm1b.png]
handl


### Step 2

Take servos with ID 31 (left arm) and ID 41 (right arm) and unscrew the 4 screws that are at the bottom of the servo:

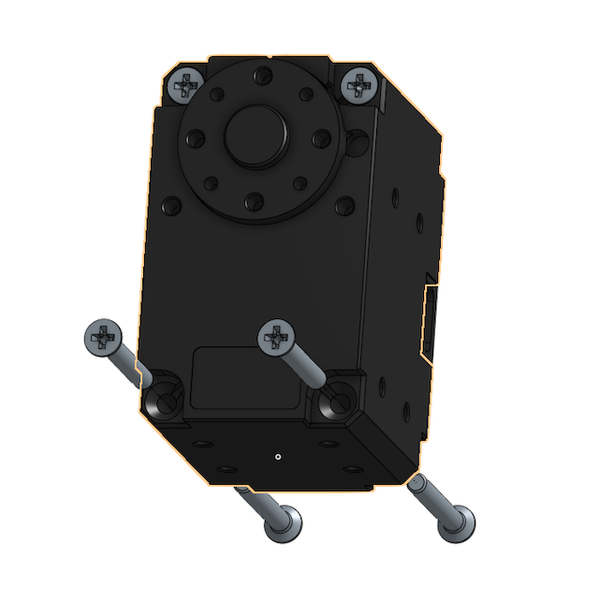
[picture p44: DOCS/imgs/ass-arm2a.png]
XLscrews


Assemble the F03 frame (with the hand) on the bottom of the servo making sure that it's oriented with the active horn on the outside of the hand (and the idle on the same side as the palm of the hand). Screw back the 4 screws, fixing the hand assembly on the servo.

For the left hand the orientation is the following:

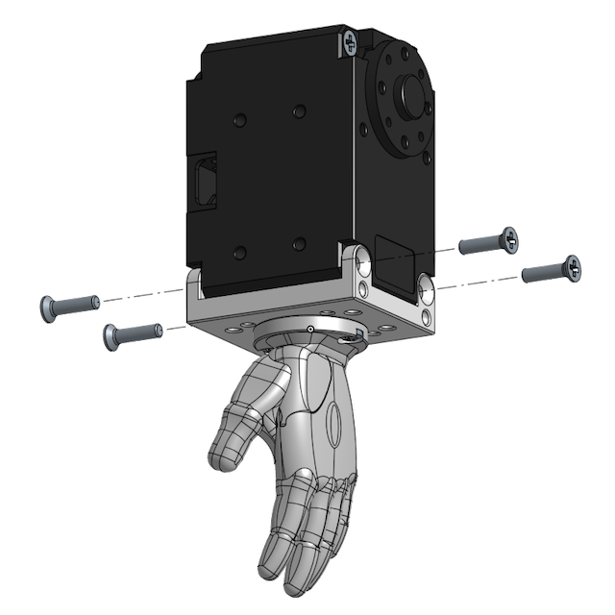
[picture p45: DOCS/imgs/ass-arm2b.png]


For the right hand the orientation is the following:

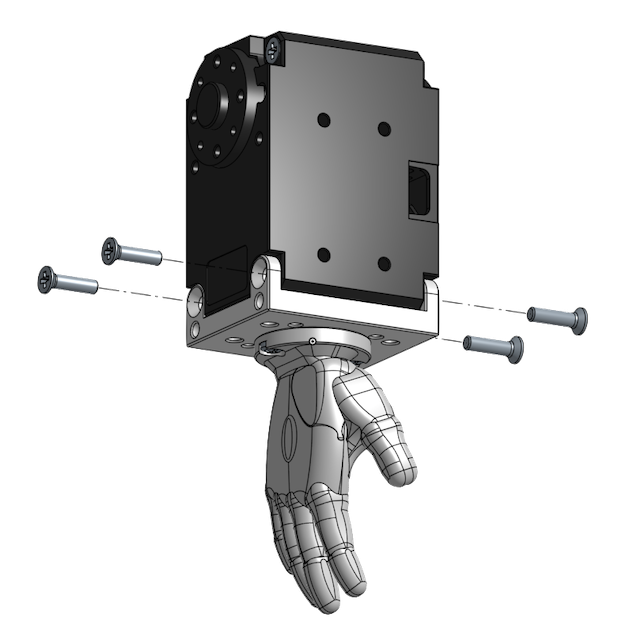
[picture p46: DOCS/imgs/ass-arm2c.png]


Connect an 100mm cable through the idle as explained in the [instructions](https://emanual.robotis.com/docs/en/dxl/x/xl430-w250/#idler-horn-assembly) for XL430.

### Step 3

Take an [F02 frame](../STL/MH5-F02.stl) and an [F03 frame](/STL/MH5-F03.stl) and connect them using 4 M2 screws and 4 nuts as shown in the image bellow:

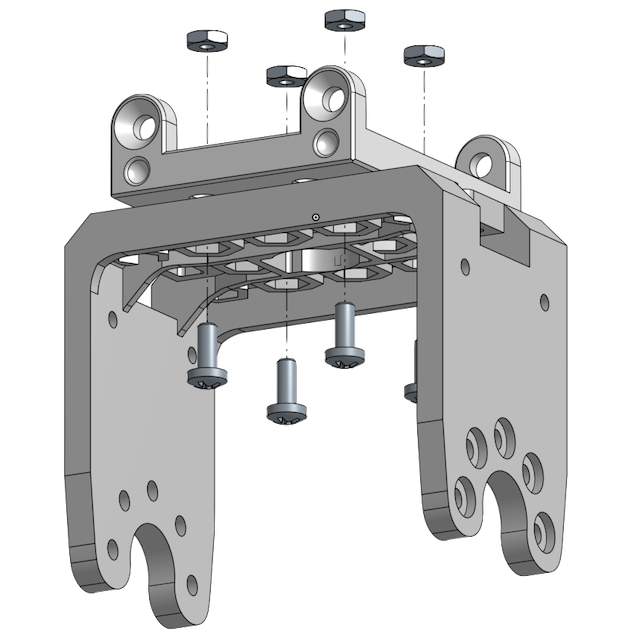
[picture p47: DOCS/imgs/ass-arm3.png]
middle arm


### Step 4

Take servo with ID 32(left arm) and ID 42 (right arm) and unscrew the 4 screws at the bottom, similar to Step 2. Mount the servo onto the F03 frame from the previous assembly. Screw back the 4 screws thus securing the servo onto the arm assembly.

Use a [F03](../STL/MH5-F03.stl) frame and assemble it on the horn of the new servo using 4 M2x5 screws as shown in the image bellow.

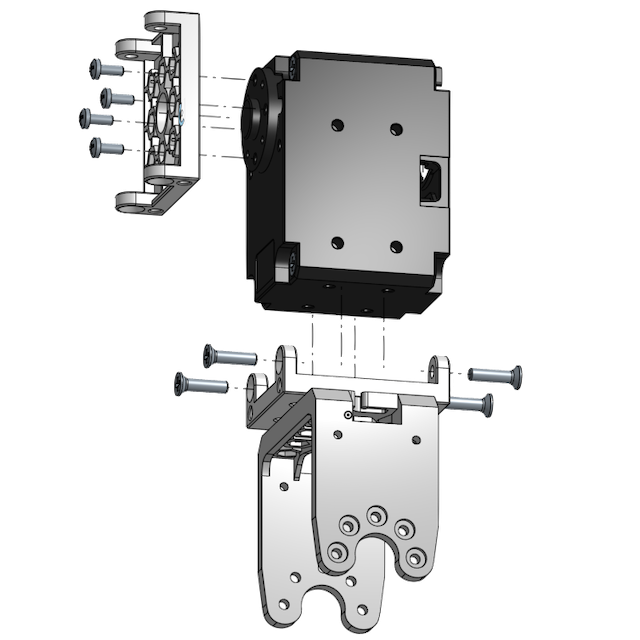
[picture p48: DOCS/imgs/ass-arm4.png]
midarm servo


### Step 5

Take servo ID 33 (left arm) or ID 43 (right arm) and unscrew the 4 screws at the bottom, as before. Place the servo over the F03 frame that was assembled on the horn of the servo ID (32/42) making sure that the front of the servo (the active horn) is facing forward. Screw back the 4 screws, thus securing the servo in place.

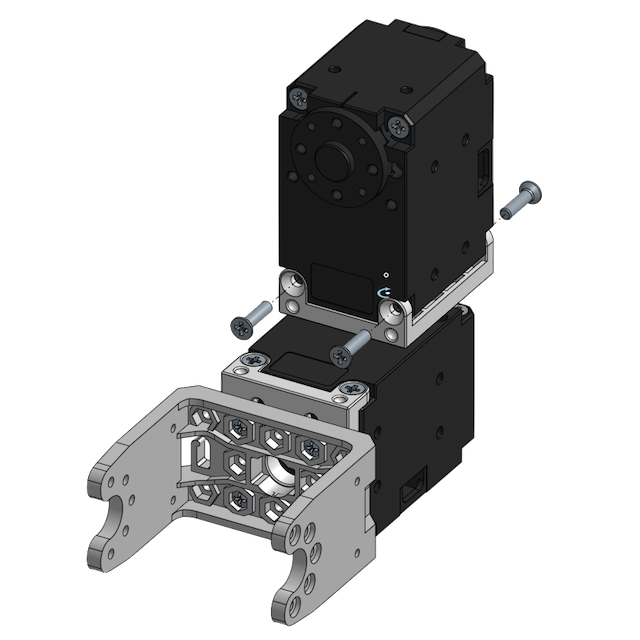
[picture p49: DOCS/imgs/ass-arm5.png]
elbow full


Remove the cover on the back of both servos and connect a 100mm cable from the lower servo (ID 32/42) to the upper servo (ID 33/43) using the connectors on the outside of the arm: for left arm use the connectors on the right as seen in the image above, for right arm use the connectors on the left.

### Step 6

Assemble the lower part of the arm (with the hand) onto the elbow assembly. The horn of the servo 31/41 will be oriented towards the outside of the arm and the palm should face the inside of it.

For left arm the assembly will be like this:

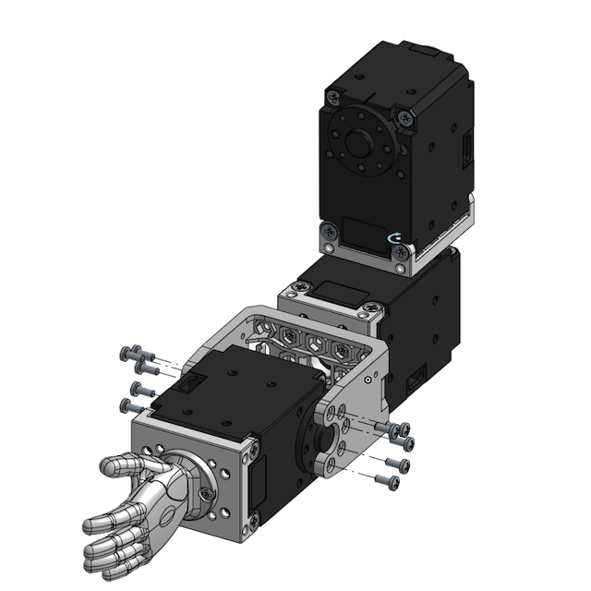
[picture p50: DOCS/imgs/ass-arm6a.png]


And for the right arm:

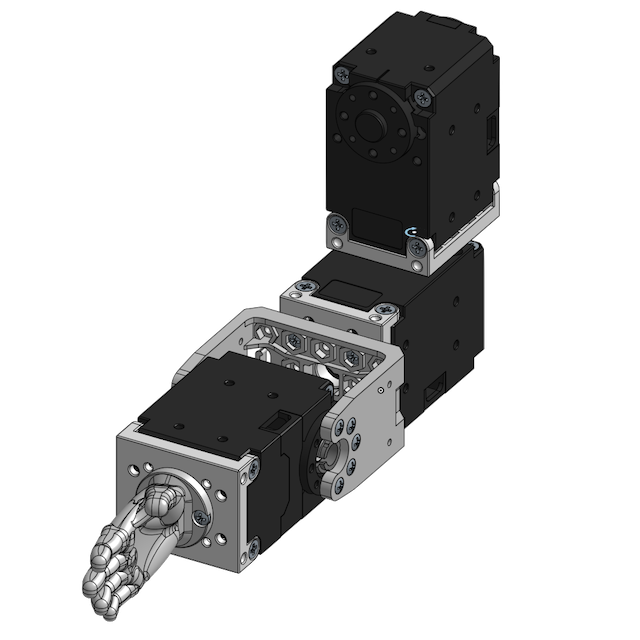
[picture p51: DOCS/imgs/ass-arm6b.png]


Take the second end of the short 100mm cable you installed at Step 2 on the servo ID 31/41 and connect it to the servo ID 32/42 on the same side (should be on the inside of the arm). Route the cable through the clamp that is provided in the frame F03 placing one cable at a time and following the order of the cables so that they are aligned naturally. You can now replace the cover over the connectors for the servo ID 32/42.

### Step 7

Take the servo 34 (left arm) or 44 (right arm) and a frame [F04 Frame](/STL/MH5-F04.stl) and assemble it using 4 M2 screws onto the horn of the servo so that the frame points downwards:

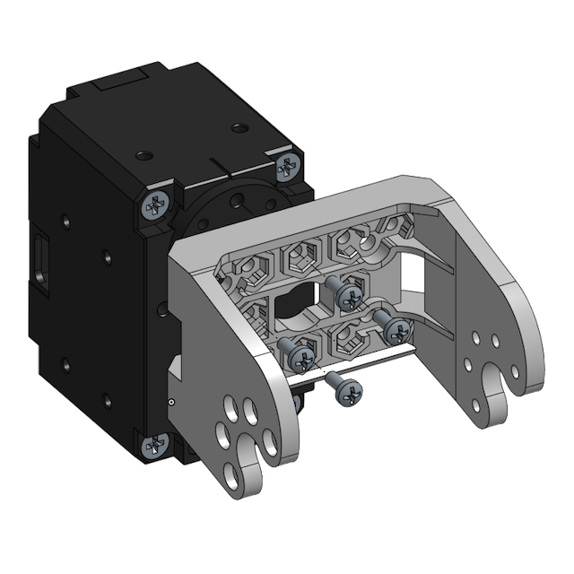
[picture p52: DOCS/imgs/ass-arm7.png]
shoulder
!

### Step 8

Connect an 180mm cable through the horn of the servo ID 33/43 and replace the cable cover on this servo.

Then assemble the shoulder with the rest of the arm paying attention to the orientation of the arm using 5 screws on the active horn side and 5 on the idle side. For left arm the position of the subassemblies if the following:

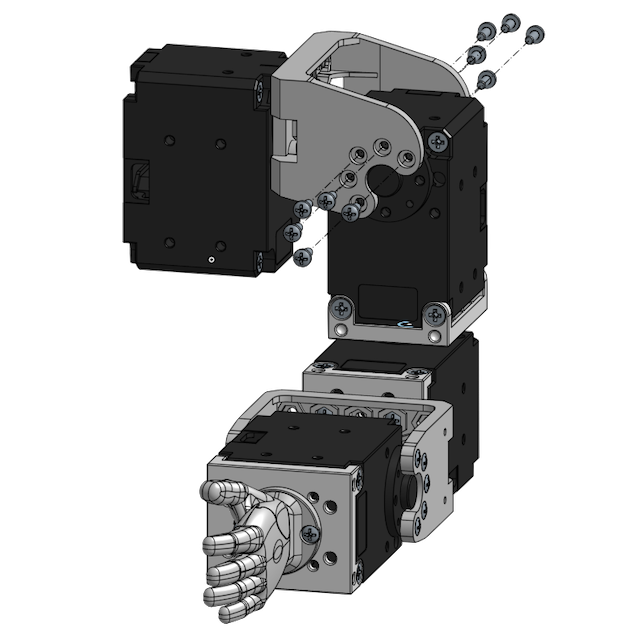
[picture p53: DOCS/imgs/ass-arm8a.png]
left arm full


For the right arm the final positioning will be like:

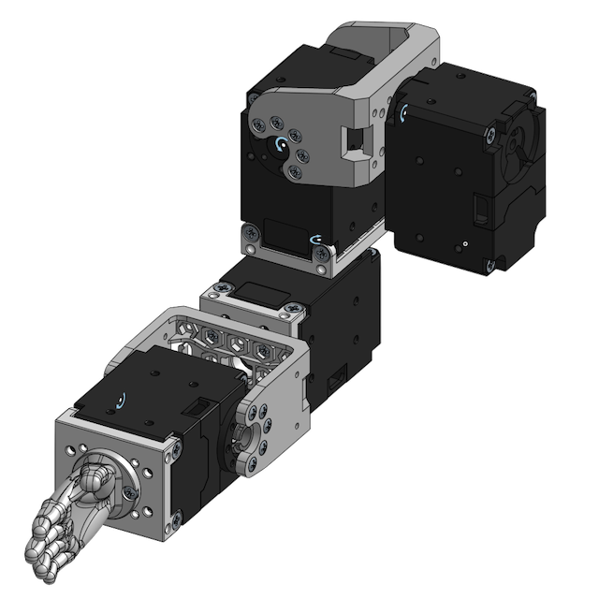
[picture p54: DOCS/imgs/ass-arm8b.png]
right arm full


Connect the cable from the servo ID 33/43 to the servo ID 34/44 using the connector towards the back (opposite in respect to how the hand is pointing). You do not need to route the cable any specific way. Connect a short 100mm cable from the remaining connector of ID 34/44 (this will connect to the HAT board) and replace the cable cover.

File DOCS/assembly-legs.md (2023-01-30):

# Leg Assembly

Left and right legs are identical with the exception of the way the ankle frames are fixed to the upper foot. Therefore the explanations bellow should be assumed to apply for both legs except for those cases when explicit instructions are given for left and right leg separately.

> **Note:**
>
> To avoid any confusions, *left* and *right* are used to refer to the part of robot from its own point of view and not from the point of view of the external observer (left leg is not the leg that we see on the left side when looking at the robot, but the leg that the robot will consider at hers left leg).

## Foot assembly

### Step 1

Install 4 heat-serts into the [Foot Top](/STL/Foot-Top.stl) as described in the the [Heat-serts](assembly-heatserts.md) section.

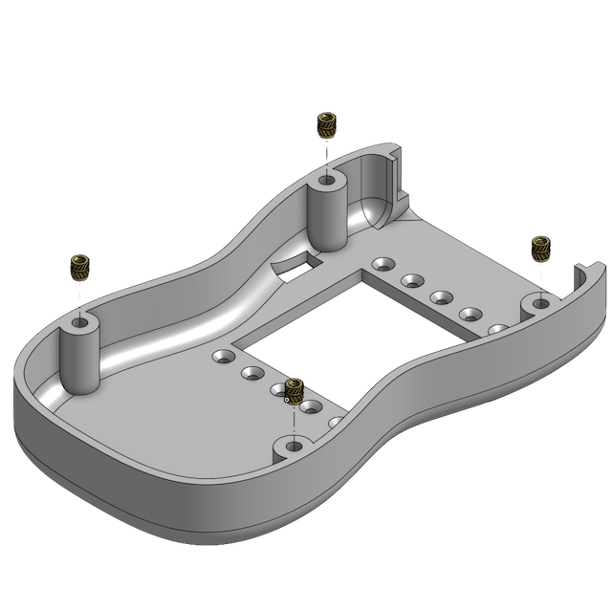
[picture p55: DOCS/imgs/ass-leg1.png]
Picture with 4 heatserts in the foot


### Step 2

Install 3 heart-serts in each of the 2 [Ankle Brackets](/STL/Ankle.stl) that we use for each foot.

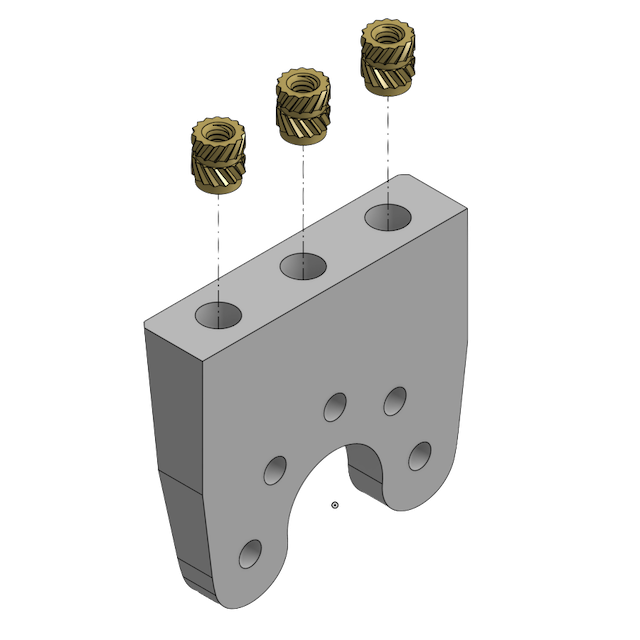
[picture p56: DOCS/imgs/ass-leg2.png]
Picture with 3 headserts in the ankle


### Step 3

Install the magnets in the [Foot Back](/STL/Foot-Back.stl) and [Foot Top](/STL/Foot-Top.stl). They are installed by glueing with superglue but you have to pay attention to the orientation of the magnets so that the backs fit properly and can be swapped if necessarily:

* take one of the foot back parts and place a single drop of superglue in one of the magnet supports. Using tweezers place a magnet in the support paying attention to the orientation: the smallest side (2mm) should be positioned facing up and the 3mm side should be facing towards you in the picture:

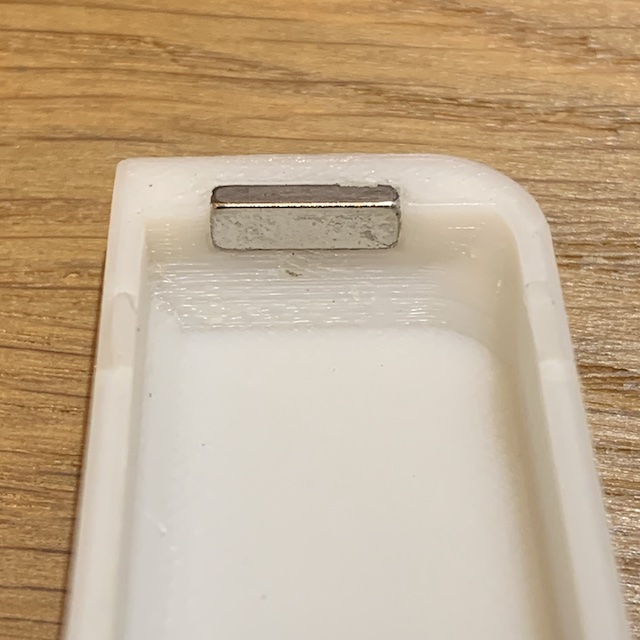
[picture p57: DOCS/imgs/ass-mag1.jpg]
MagnetInstall1


Once the glue is dried, place another magnet on the one that is already glued. It will orient itself correctly to the already glued one, but make sure that is aligned correctly with the 3mm side facing you:

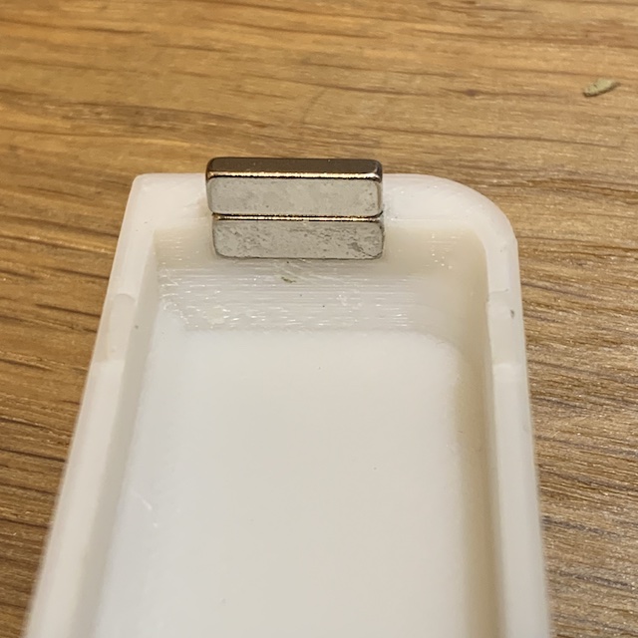
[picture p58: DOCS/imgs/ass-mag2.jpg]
MagnetInstall2


Place the Foot Top upside down and test how the magnet will be positioned:

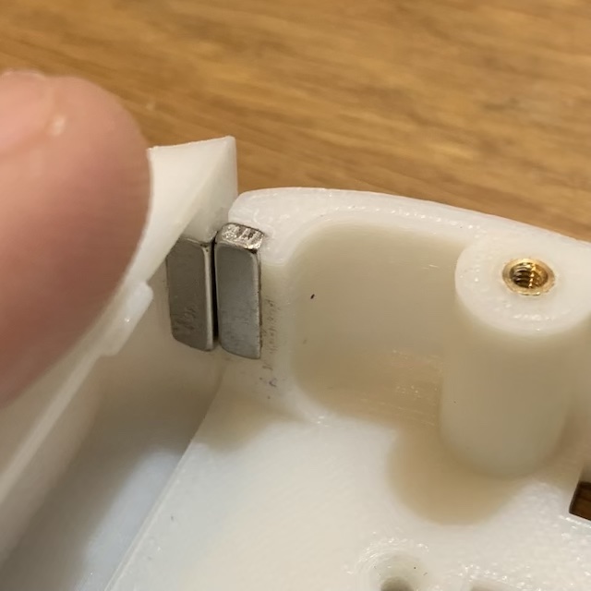
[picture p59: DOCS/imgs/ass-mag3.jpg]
MagnetInstall3


If you're happy with the placement and orientation of the magnet, remove them from the Foot Top, then place a single drop of superglue in the Foot Top magnet holder and quickly re-apply the magnets as in the picture above, but this time with a very fast movement slide the Back Cover forward while holding the magnet that needs to be glued on the Foot Top with your thumb:

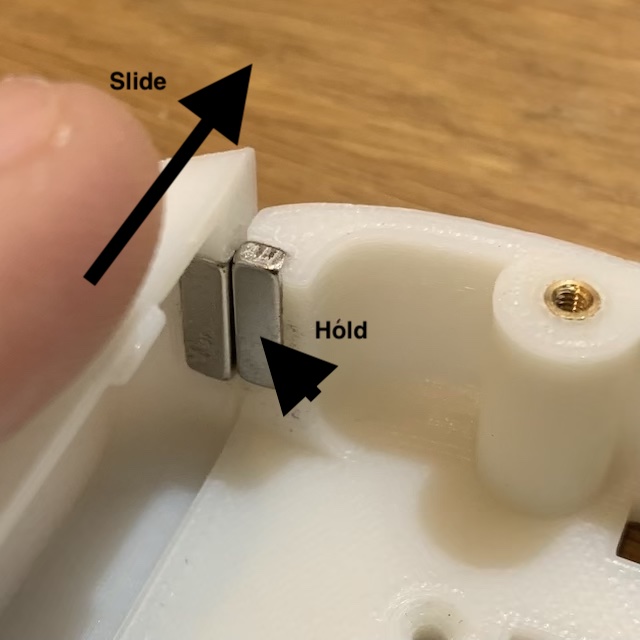
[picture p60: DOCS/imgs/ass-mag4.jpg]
MagnetInstall4


This should keep the magnet in place and ensure that they are positioned correctly.

Now add one more magnet on the same glued magnet on the Foot Back like in the earlier picture and, keeping the same orientation of the Back Foot part verify the placement on the other magnet position on the Foot Top:

MagnetInstall5

Again, if everything is looking right, remove them from the Foot Top, place  single drop of superglue in the Foot Top magnet holder and re-apply the magnets and with a sharp movement slide the Back cover towards you this time, while holding the magnet to be glued in place with the other hand.

The last thing now is to mount the second magnet on the Foot Back. You place a new magnet on the Foot Top last placed magnet:

MagnetInstall6

Put a single drop of superglue on the remaining magnet holder in the Foot Back, approach it to the magnets and, while holding the last magnet with a finger, slide the back upward.

After all the magnets are glued make sure that the back part is matching correctly with the Foot Top and that removal and re-attaching is firm.

To apply the magnets for the second foot, use the back part with the magnets that you created earlier and place a new magnet on one side then glue it with the same technique onto the new Foot Top part. Then place on the other side and glue it on the other side of the Foot Top. Make sure during this time that the Foot Back is positioned correctly in respect to the Foot Top.

When the second Foot Top has the magnets in place you can use it to glue the magnets on the second Foot Back. First place a new magnet on one of the sides of the Foot Top, then glue it on the corresponding side of the second Foot Back. The place the last magnet on the other side of the Foot Top and glue it on the remaining side of the Foot Back.

### Step 4

You can now screw the two ankle frames onto the Foot Top. The parts need to be located on the inside of the leg as shown in this picture:

ass-leg-4

The ankle frames are not perfectly straight. Instead one of the vertical faces has a draft that is supposed to be oriented towards the exterior of the foot (that is towards the front for the frame that is connected in the front and towards the back for the frame that is connected on the back). Use 3 M2 screws to fix the front ankle and 3 M2 screws to fix the back ankle frame.

foot with both ankles

### Step 5

Now place the FSR circuit board on the Foot Sole. The board should be a close fit and should sit on the margin that is specifically cut into the sole. The bumpers of from the FSR resistors should come out very slightly through the 4 large holes in the sole and the back of the circuit board should be flush with the rest of the sole on the upper side.

foot sole with the PCB installed

Using 4 M2 screws assemble the Foot Top and then Foot Sole producing the lower part of the foot.

foot assembly

The finalized left foot will look like this:

left foot image

And the right foot will be like this:

right foot image

### Step 6

We will no assemble the main foot parts. The following steps are similar for left and right foot, the only difference are the servos used. We will refer to these servos by their IDs indicating both left/right codes  as 11/21.

Use the dual servo for the knee with IDs 13/23 and 14/24. Take one Straight U frame [MH5-F02](../STL/MH5-F02.stl) and assemble it using 4 M2 screws onto the active horn A (13/23). Make sure that the horn is at 0 position and that in this position the F02 frame is perpendicular to the servo:

knee with F02

Install a 180mm cable [through the idle](https://emanual.robotis.com/docs/en/dxl/x/2xl430-w250/#idler-horn-assembly) for the axis B labeled with ID 14/24.

### Step 7

We will now mount the ankle servo IDs 11/21 and 12/22.

Follow the instructions about [installing cables through the idle](https://emanual.robotis.com/docs/en/dxl/x/2xl430-w250/#idler-horn-assembly) and install a 100mm cable on the side with the horn A for ID 11/21 and an 180mm cable on the side with the horn B for ID 12/22. Double check that both active horns are in the 0 position.

Place the frame F2 mounted earlier over axis B of this new servo. The second axis of the knee servo (ID 14/24) should be towards the back. Use 5 screws to connect the F02 frame to the active horn of the axis B of the ankle and 5 more to connect the idle on the other side.

ankle and knee servos connected

### Step 8

Slide the 180mm cable from the ankle through the lateral holes in the F02 on one side, then get the cable out on the other side of the frame. Connect it to the free connector on the knee servo.

knee cable routing and connection

### Step 9

Make sure that the horn for axis B of the knee servo is in position 0. We will mount the frame [F05](../STL/MH5-F05.stl) onto this axis. You will need to pay attention to the orientation as this is one of the frames that needs to be mounted in an offset position.

Place the thigh frame (F05) as shown in the bellow image. Pay attention on the position of the active horn relative to the frame. The B axis of the knee servo should show one indentation line on the edge of the horn on the upper side of the servo. That is the indicator that the horn is at 0 position. Use 5 M2 screws to fasten the frame in position, then another 5 on the other side to fasten the idle horn.

Thigh assembly

Once the frame is secured in place, rotate the horn by gently turning it anti-clockwise (in the above picture) so that the thigh is oriented vertically above the rest of the leg.

Thigh positioned

### Step 10

This step requires a little more attention. You should take the cable from the knee servo that is connected through the idle of B axis (ID 14/24) and [wire it through the idle](https://emanual.robotis.com/docs/en/dxl/x/2xl430-w250/#idler-horn-assembly) of the A axis of the hip servo (IDs 15/25). You might choose to let the cable unconnected to the servo JST connector to allow for a tight adjustment of the cable later, but this is not mandatory.

After the cables are in palace, mount the servo A axis on the thigh frame F05 so that the servo is is positioned vertically and the horn of B axis is towards the front. Secure the servo in place with 5 M2 screws on the horn side and 5 M2 screws on the idle side.

Hip servo connected

If necessary you can adjust the cable between the knee and hip by pulling some of the length through the horn idle to reduce the amount of cable that is on the side of the thigh frame. You can then cut the existing JST-EH connector so remove the extraneous lenght of cable and re-crimp a new connector.

> **Warning**
>
> When trimming cables, **do not** cut all wires in one go! It will be very hard to identify the cables after that. Instead cut one cable at a time, remove the insulation with an appropriate cable stripper, crimp a new pin and place it in a new JST EH housing in the same position as the original. Then move to the next cable.

Finally use a cable clip on the side of the thigh to keep the cable for interfering with the frame movements.

Thigh cable

### Step 11

You should repeat the steps 6-10 to assemble the other leg.

Once both legs are assembled you can mount them on the previously assembled feet. Place the servo axis A (ID 11/21) on the ankle frames of the foot with the active horn towards the front of the foot and the 100mm cable coming from the idle towards the back.

Use 5 M2 screws to fix the front (active horn) and then anther 5 screws to fix the idler on the back ankle.

lower servo mounted on foot

The 100mm cable from the leg should be routed in the JST connector in the foot on the outside part of the leg.

### Foot Review

This concludes the construction of the legs. The following figures reflect the fully assembled legs.

Front view:

Full legs)

Side view:

Full legs)

Back view:

Full legs)

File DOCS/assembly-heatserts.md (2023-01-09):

# Heat Serts

Some of the assemblies in MH5 use brass heat-serts that need to be securely inserted in the 3D printed parts. The following list shows these parts and the number of heat-serts needed:

* upper part of the foot [Foot-Top.stl](../STL/Foot-Top.stl) uses 4 heat serts for fastening of the sole
* ankle braket [Ankle.stl](../STL/Ankle.stl) uses 3 heat serts for each bracket (there are 2 brakets for each foot)
* neck [Neck.stl](../STL/Neck.stl) uses 3 heat serts for fastening to the cheast

All heat-serts are M2x3.9mm, and they have a recommended 3.1mm mounting hole.

They are pressed into the 3D printed parts using a normal soldering iron with temperature control. Chose a relatively large conic tip that will fit snugly the heat sert:



The idea is that the tip should enter relatively easy into the threaded insert, but provide enough friction so that it stays on the tip when held vertically:



Make sure that the tip is clean of any solder or flux. Start the soldering station and set the temperature to 150 degrees Celsius. You might have to experiment with the temperature setting depending on the characteristics of the material the 3D print used. In principle you want a temperature high enough that the plastic becomes slightly malleable, but low enough not excessively melt the part and distort it. The right temperature is reached when you wil feel the insert finding its way into the part with just a slight degree of pressure and without producing any warping of the surrounding walls of the 3D printed part.

Once the tip has reached the desired temperature, use some tweezers to place a heat sert on the tip and then, keeping the soldering iron as vertical as possible align it with the hole in the 3D part:



Wait about 10-15 seconds so that the hear-sert is hot and the plastic starts to soften, then apply a small amount of pressure to insert it. If you can't lower the brass insert or you must apply too much force, it means the temperature is too low. Increase it by 5-10 degrees and after waiting for a little bit to be transmitted to the parts, try again to insert the heat-sert. If you hear hissing noises, see fumes or the plastic starts to melt around the heat-sert, the temperature is too high. Reduce it by 10 degrees, wait for the tip to reduce it's temperature and try again.

You should push the heat-sert all the way in the mounting hole and then an extra 0.5-1mm bellow the top of the hole. This is needed, because when you will pull up the solder tip, the heat-serts will tend to bounce back slightly.



During the pressing of the heat-sert make sure the the soldering iron is as vertical as possible. If you notice any deviation you can re-align the insert by over-compensating the position of the soldering iron and gently re-orient the brass insert.

Once the part is placed fully in the hole, lift the soldering iron and let the parts cool down. If you want you can continue inserting the other parts. Once cooled down inspect the joint and make sure that you flatten any possible burrs that might be produced by the heat-sert making its way into the plastic by using some sand paper or a file. Is it very important that the top of the hole is perfectly flat so that when fastened with the other parts there are no gaps or untrue surfaces.



You should also test that an M2 screw fits comfortably into the heat-sert and that there are no obstructions on the thread produced by the melting plastic. Sometimes the bottom of the hole might include some molten plastic that stops the screw for screwing in the desired length (in general most screws need only 3 to 3.5mm to screw in and you should not have these types of issues). In this case you can use a 1.5mm drill bit to carefully remove the plastic on the bottom of the hole, making sure that it is perfectly parallel with the insert and that you do not damage the thread.

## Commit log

2022-08-22 rev E
    [Ankle.stl, Foot-Back.stl, Foot-Sole.stl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]
2022-09-14 Updated sole and foot with new FSR
    [Foot-Sole.stl]
2022-10-06 Rev F head
    [Head-Back.stl, Head-Camera-Cover.stl, Neck.stl]
2022-10-06 Update README.md
    Finalised head using Waveshare cameras and reduced size.
2023-01-09 updates to servo config
2023-01-09 heat-serts instructions
2023-01-09 added picture with all servo IDs
2023-01-09 leg assembly first draft
2023-01-13 finalize legs assembly
2023-01-13 arms assembly
2023-01-20 leg assembly pictures
2023-01-30 leg assembly updates
2023-01-30 final images leg assembly
2023-02-01 arm assembly updates
2023-02-05 torso assembly updates
2023-02-06 full assembly instructions
